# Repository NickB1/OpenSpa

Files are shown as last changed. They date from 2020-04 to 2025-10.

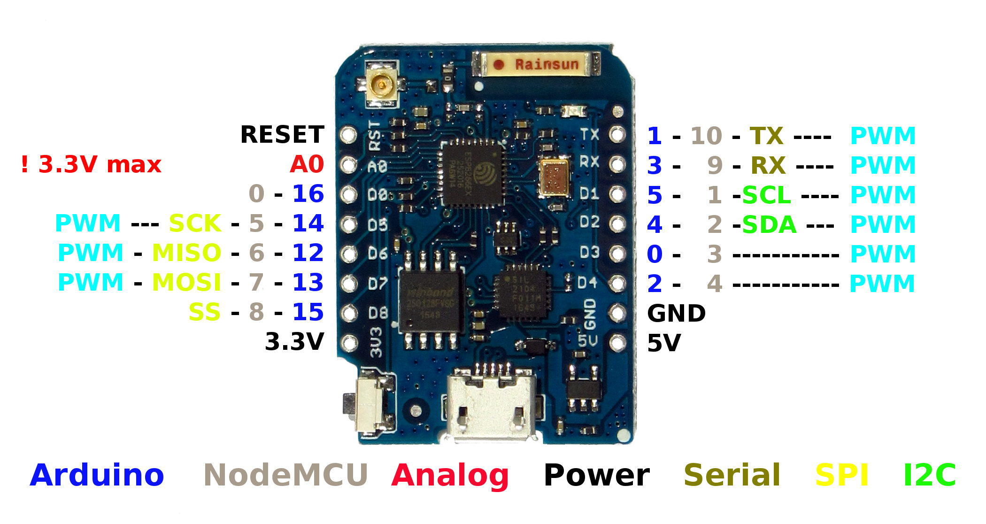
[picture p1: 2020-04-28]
documents/Wemos/Wemos_D1_Mini_Pro_Pinout.jpg

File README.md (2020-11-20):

# OpenSpa
An open source hot tub controller using the ESP8266 (WeMos).

works with MQTT Homie (https://homieiot.github.io/)

Built on ESP8266 Arduino core v2.7.0

More information: https://hackaday.io/project/171003-openspa

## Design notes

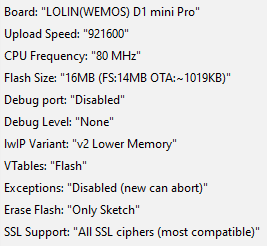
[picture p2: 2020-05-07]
firmware/_openspa/esp8266 settings/OpenSpa_esp8266_settings.png

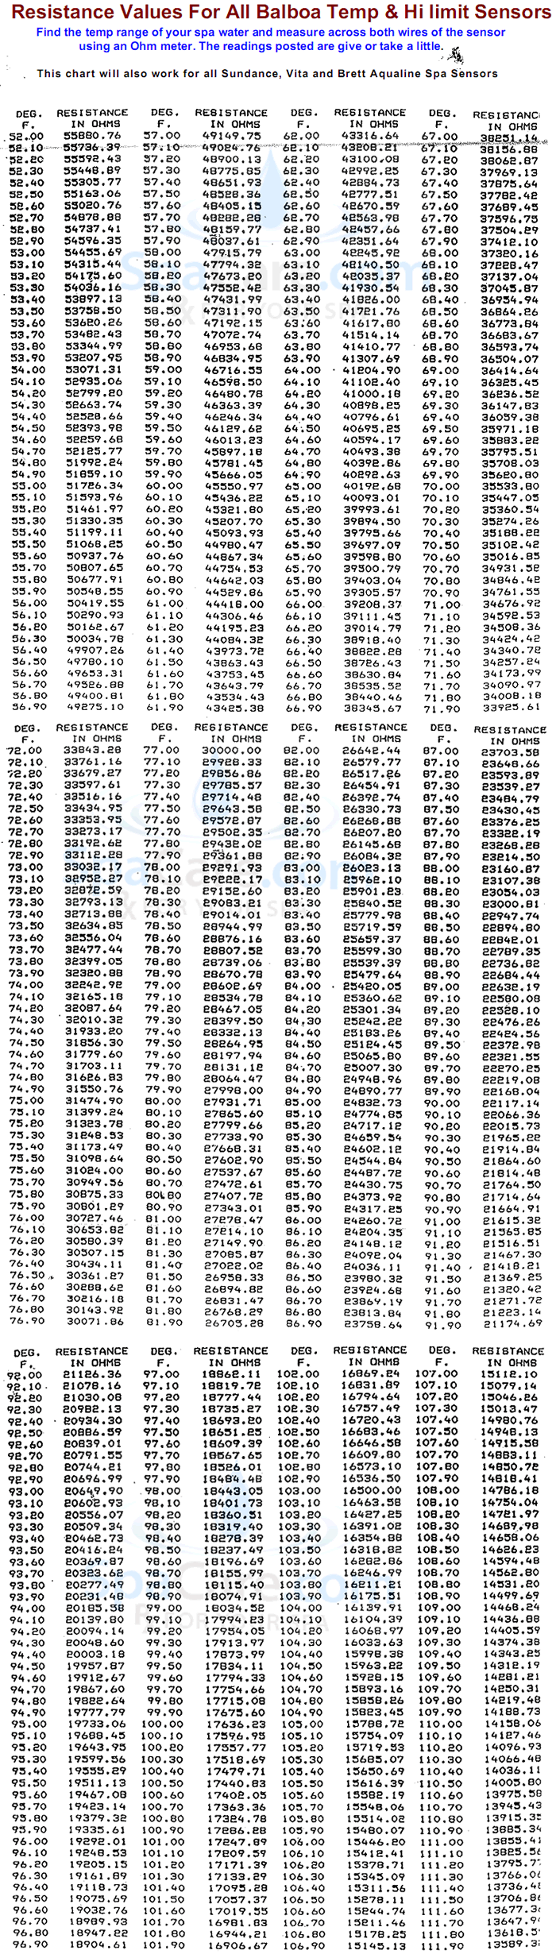
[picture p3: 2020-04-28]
documents/Balboa/Balboa_Resistance_Chart.gif

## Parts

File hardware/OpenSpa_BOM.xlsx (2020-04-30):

Designator | Value | Manufacturer | Part Number | Package | Quantity
C1, C2, C3, C4, C5, C6, C7, C8, C9, C10, C11, C14, C15, C17, C22, C23, C24 | 0.1uF | Kemet | C0603C104K3RAC7411 | 0603 | 17
C12, C21 | 1uF | Kemet | C0603C105K4PACTU | 0603 | 2
C13, C16 | 10uF | Murata | GRT31CR61H106KE01L | 1206 | 2
C18, C19 | 22uF | Kemet | C1206C226M8RACTU | 1206 | 2
C20 | 75pF | Kemet | C0603C750J5GACTU | 0603 | 1
CON1 |  | Wurth Elektronik | 615008143721 | TH | 1
CON2, CON3, CON4, CON5 |  | Wurth Elektronik | 691236510003 x 3 | TH | 4
D1 |  | ON Semiconductor | BAT54T1G | SOD-123 | 1
D2 |  | Diodes Incorporated | B160-13-F | DO-214AC | 1
D3, D4 |  |  | DNP |  | 2
L1 | 15uH | Wurth Elektronik | 7447714150 | 1050 | 1
LED1, LED3 | Green | Wurth Elektronik | 150080VS75000 | 0805 | 2
LED2 | Red | Wurth Elektronik | 150080RS75000 | 0805 | 1
P1 | 10.0K | Bourns | 3296W-1-103LF | 3296 | 1
Q1 |  | Vishay | SUD50N04-8M8P-4GE3 | TO-252 | 1
R1, R2, R4, R5, R6, R7, R11, R14 | 5.10K | Vishay | CRCW06035K10FKEA | 0603 | 8
R3, R10, R15, R27 | 10.0K | Vishay | CRCW060310K0FKEAHP. | 0603 | 4
R8 | 100K | Vishay | CRCW0603100KFKEAHP | 0603 | 1
R9, R19, R23, R24, R25, R26 | 1.00K | Vishay | CRCW06031K00JNEA | 0603 | 6
R12, R13, R16, R17, R20 | 2.20K | Vishay | CRCW06032K20FKEA | 0603 | 5
R18 | 49.9E | Vishay | CRCW060349R9FKEA | 0603 | 1
R21 | 100K | Vishay | CRCW0603100KFKEA | 0603 | 1
R22 | 13.3K | Vishay | CRCW060313K3FKEA | 0603 | 1
SW1 |  | TE Connectivity | 1825910-6 | TH | 1
U1, U3 |  | Texas Instruments | LM321MF/NOPB | SOT-23-5 | 2
U2 |  | Texas Instruments | TL331IDBVR | SOT-23-5 | 1
U4, U5, U6 |  | Texas Instruments | SN74LVC1G125DCK | SC-70-5, SC-88A, SOT-323-5, SOT-353, 5-TSSOP | 3
U7 |  | Texas Instruments | PCA9515BDGKR | VSSOP-8 | 1
U8 |  | Microchip | MCP23017T-E/SO | SOIC-28 | 1
U9 |  | Microchip | MCP1700T-3302E/TT | SOT-23-3 | 1
U10 |  | Wemos | D1 mini Pro |  | 1
U11 | Original: TI SN74LVC1G02DBV | Nexperia | 74LVC1G02GV,125 | SC-74A-5 | 1
U12 |  | Texas Instruments | TPS54308DDCT | TSOT-23-6 | 1
U13 |  | Texas Instruments | ULN2803ADWR | SOIC-16 | 1
U14 |  | Texas Instruments | TXS0101DBVR | SOT-23-6 | 1
U15 |  | Maxim | DS18B20+ | TO-92 | 1

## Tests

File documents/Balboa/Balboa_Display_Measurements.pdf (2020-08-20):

# Balboa Display

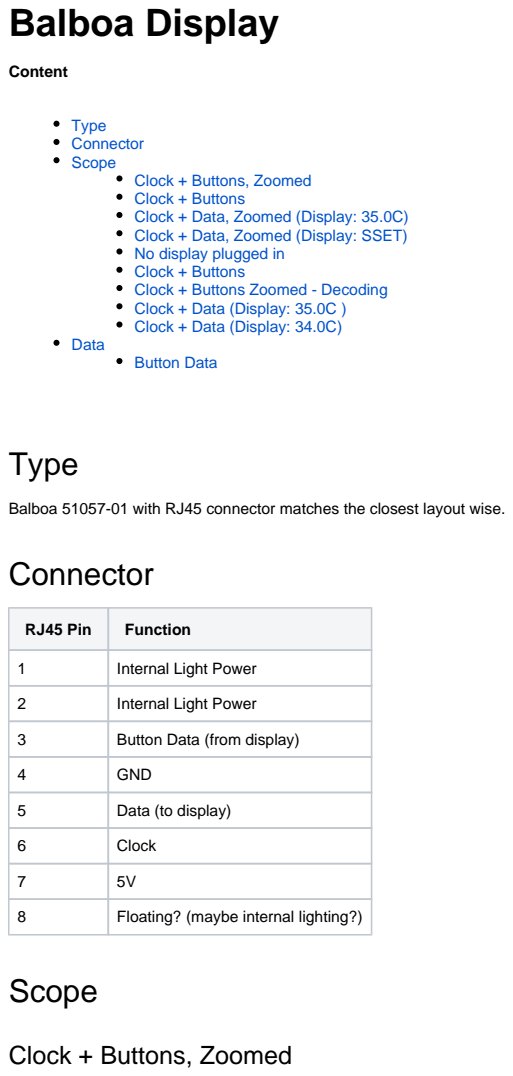
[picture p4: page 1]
Content; Type Connector Scope; Data; Button Data; Type; RJ45 Pin; Function; Internal Light Power; Button Data (from display); GND; Data (to display); Clock; Floating? (maybe internal lighting?); Scope

Clock + Buttons, Zoomed
Clock + Buttons
Clock + Data, Zoomed (Display: 35.0C)
Clock + Data, Zoomed (Display: SSET)
No display plugged in
Clock + Buttons Zoomed - Decoding
Clock + Data (Display: 35.0C )
Clock + Data (Display: 34.0C)

Balboa 51057-01 with RJ45 connector matches the closest layout wise.
Connector

## Clock + Buttons

## Clock + Data, Zoomed (Display: 35.0C)

## Clock + Data, Zoomed (Display: SSET)

## No display plugged in

## Clock + Buttons

## Clock + Buttons Zoomed - Decoding

Button | Decoding
Temp Up | 100

Temp Down 101

Light | 111
Jets | 110
Blower | 011

## Clock + Data (Display: 35.0C )

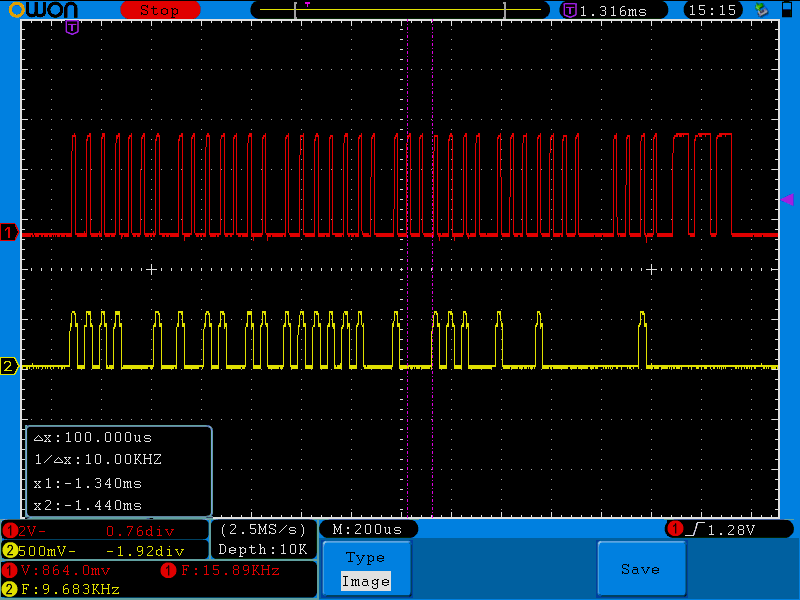
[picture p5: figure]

## Clock + Data (Display: 34.0C)

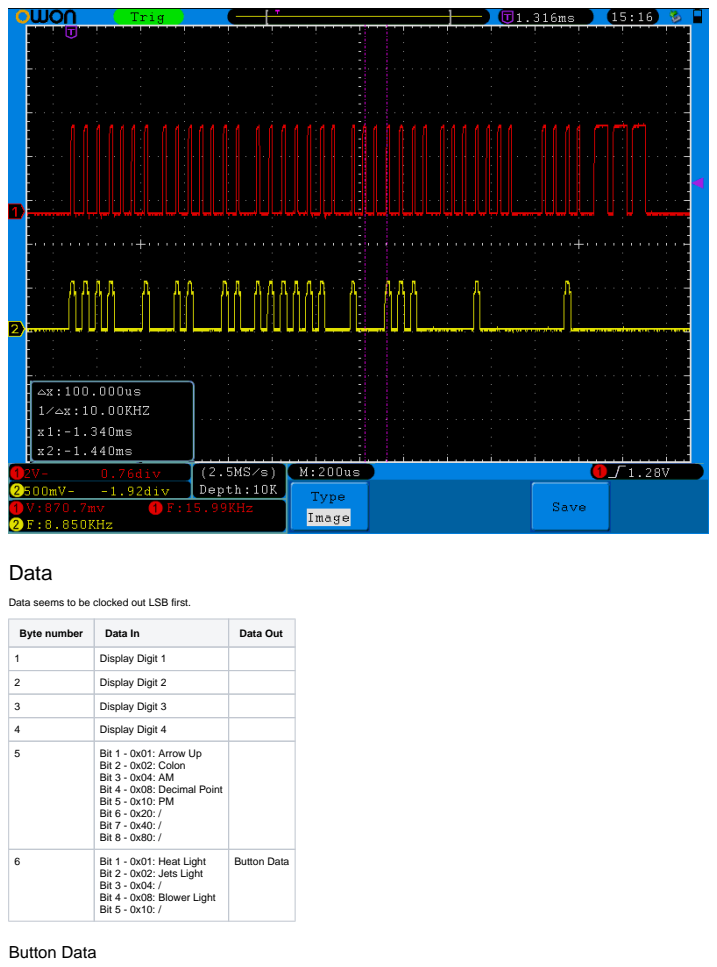
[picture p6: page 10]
Data; Byte number; Data In; Data Out; Display Digit 1; Display Digit 2; Display Digit 3; Display Digit 4; Bit 1 - 0x01: Arrow Up; Bit 1 - 0x01: Heat Light; Button Data

Data seems to be clocked out LSB first.

Bit 2 - 0x02: Colon
Bit 3 - 0x04: AM
Bit 4 - 0x08: Decimal Point
Bit 5 - 0x10: PM
Bit 6 - 0x20: /
Bit 7 - 0x40: /
Bit 8 - 0x80: /

Bit 2 - 0x02: Jets Light
Bit 3 - 0x04: /
Bit 4 - 0x08: Blower Light
Bit 5 - 0x10: /

Function | MSB First | LSB First
Temp Up | 0x04 | 0x10
Temp Down | 0x05 | 0x50
Lights (3 settings) 0x07 | 0x70
Jets (2 settings) | 0x06 | 0x30
Blower | 0x03 | 0x60

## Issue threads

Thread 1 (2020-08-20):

Question

tmjo, 2020-08-20:
Hi @NickB1,

Sorry for opening this as an issue, it's more of a question, and I hope you don't mind me asking here. I'm following your OpenSpa and also the balboa-spa-mqtt-controller projects trying to do something similar. My controller is (still) working but is a decade old. If it fails, I'll try do implement a solution similar to OpenSpa, but meanwhile I would like to connect my spa to get status and control if with an ESP8266.

My spa is a Balboa HSEX2000 Mach3 (part no 54503-01) and is branded GL2000 inside a plastic enclosure (know there is a different variant of the same with metallic enclosure). Display is ML400.

Would you mind me asking which display is connected to yours? And do you know the type of controller that was originally fit to it? I see you mentioned 25501 on hackaday.io, would you mind sharing some more details?

I was initially trying to use the information found [here](https://github.com/ccutrer/balboa_worldwide_app), but found out my spa has a 8-pin Molex connector to the display and not 4-pin as is the case for the referenced project which is RS485 based. See particularly [this issue](https://github.com/ccutrer/balboa_worldwide_app/issues/14) if you're interested. Although yours is a RJ45, I was hoping it would be similar to mine, just different connector.

Anything you could share that could help me shed some light on my issue? Protocol? Connections?

Thanks in advance.

NickB1, 2020-08-20:
Hi,

No problem.
At first glance the HSEX2000 Mach3 seems to be fairly newer then my original 25501 board.
The Balboa 51057-01 display seems to match my display the closest (the spa manufacturer has stuck another layout over it with their logo).

I've committed my findings about the display protocol in the documents folder.
It's best to leave the display plugged in and probe the lines with a scope.
My controller just outputted a single clock pulse without any data when no display was plugged in.
It waited for the data in line to go high before outputting the full clock train with data.

tmjo, 2020-08-20:
Thanks a lot! I believe this information will help me a lot in deciphering my spa. I'll try to connect a oscilloscope and measure one of the next weeks when I'm back at work and have one available. Even if the models are different, I guess they don't change the protocols every second day, so since mine is not a match with the newer series (4-pin) I really hope they are similar to yours!

Bostwickenator, 2021-10-04:
Hey Nick. I'm also looking into this wanting to emulate the panel side. I don't see in that document if this is using any kind regular serial protocol. It looks like you are just clocking out your data "by hand". I'm thinking from the scope traces it's 3V signaling? It also looks like you are commanding the display segments themselves instead of writing a temperature value and the panel using that to set the segments itself. Did I understand that correctly?

NickB1, 2021-10-05:
>
>
> Hey Nick. I'm also looking into this wanting to emulate the panel side. I don't see in that document if this is using any kind regular serial protocol. It looks like you are just clocking out your data "by hand". I'm thinking from the scope traces it's 3V signaling? It also looks like you are commanding the display segments themselves instead of writing a temperature value and the panel using that to set the segments itself. Did I understand that correctly?

Hi, you can see some scope screenshot of the protocol here:
https://github.com/NickB1/OpenSpa/blob/master/documents/Balboa/Balboa_Display_Measurements.pdf
It's not a regular uart, it's a custom data/clock protocol where individual display segments data and button data is clocked through.
Maybe newer displays use a regular uart but I don't have any experience with these.

Bostwickenator, 2021-10-05:
Thanks for the reply. I was looking at the screenshots but was having a
little trouble figuring out a few parameters for instance in (clock +
data), zoomed (display: 35.0C) there appear to be three signal levels for
the data line but I don't see any references to that in your protocol
implementation. Is that just an artifact of the scope? It looks like the
clock signal is 4V and data is only 500mV? I read the OWON scope manual it
that seems to be how I should interpret the screenshots. Those values just
seem a little odd so I thought I'd reach out and ask. Thanks for the help
of even posting this it's invaluable.

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

NickB1, 2021-10-05:
Good catch, I think the multiplier on the data channel of the scope was not configured to be the same as the probe (probable should be x10).
Both signals have a logic level of 5V.
Here is a snippet of the schematic where the level conversion to 3.3V happens to interface it with the esp8266.

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

netmindz, 2022-01-17:
The VL series isn't compatible with the GL controllers @tmjo not sure why not. So they may or may not share the same protocol. I'll have to hook up the scope and see what we get

Closed 2021-01-27.

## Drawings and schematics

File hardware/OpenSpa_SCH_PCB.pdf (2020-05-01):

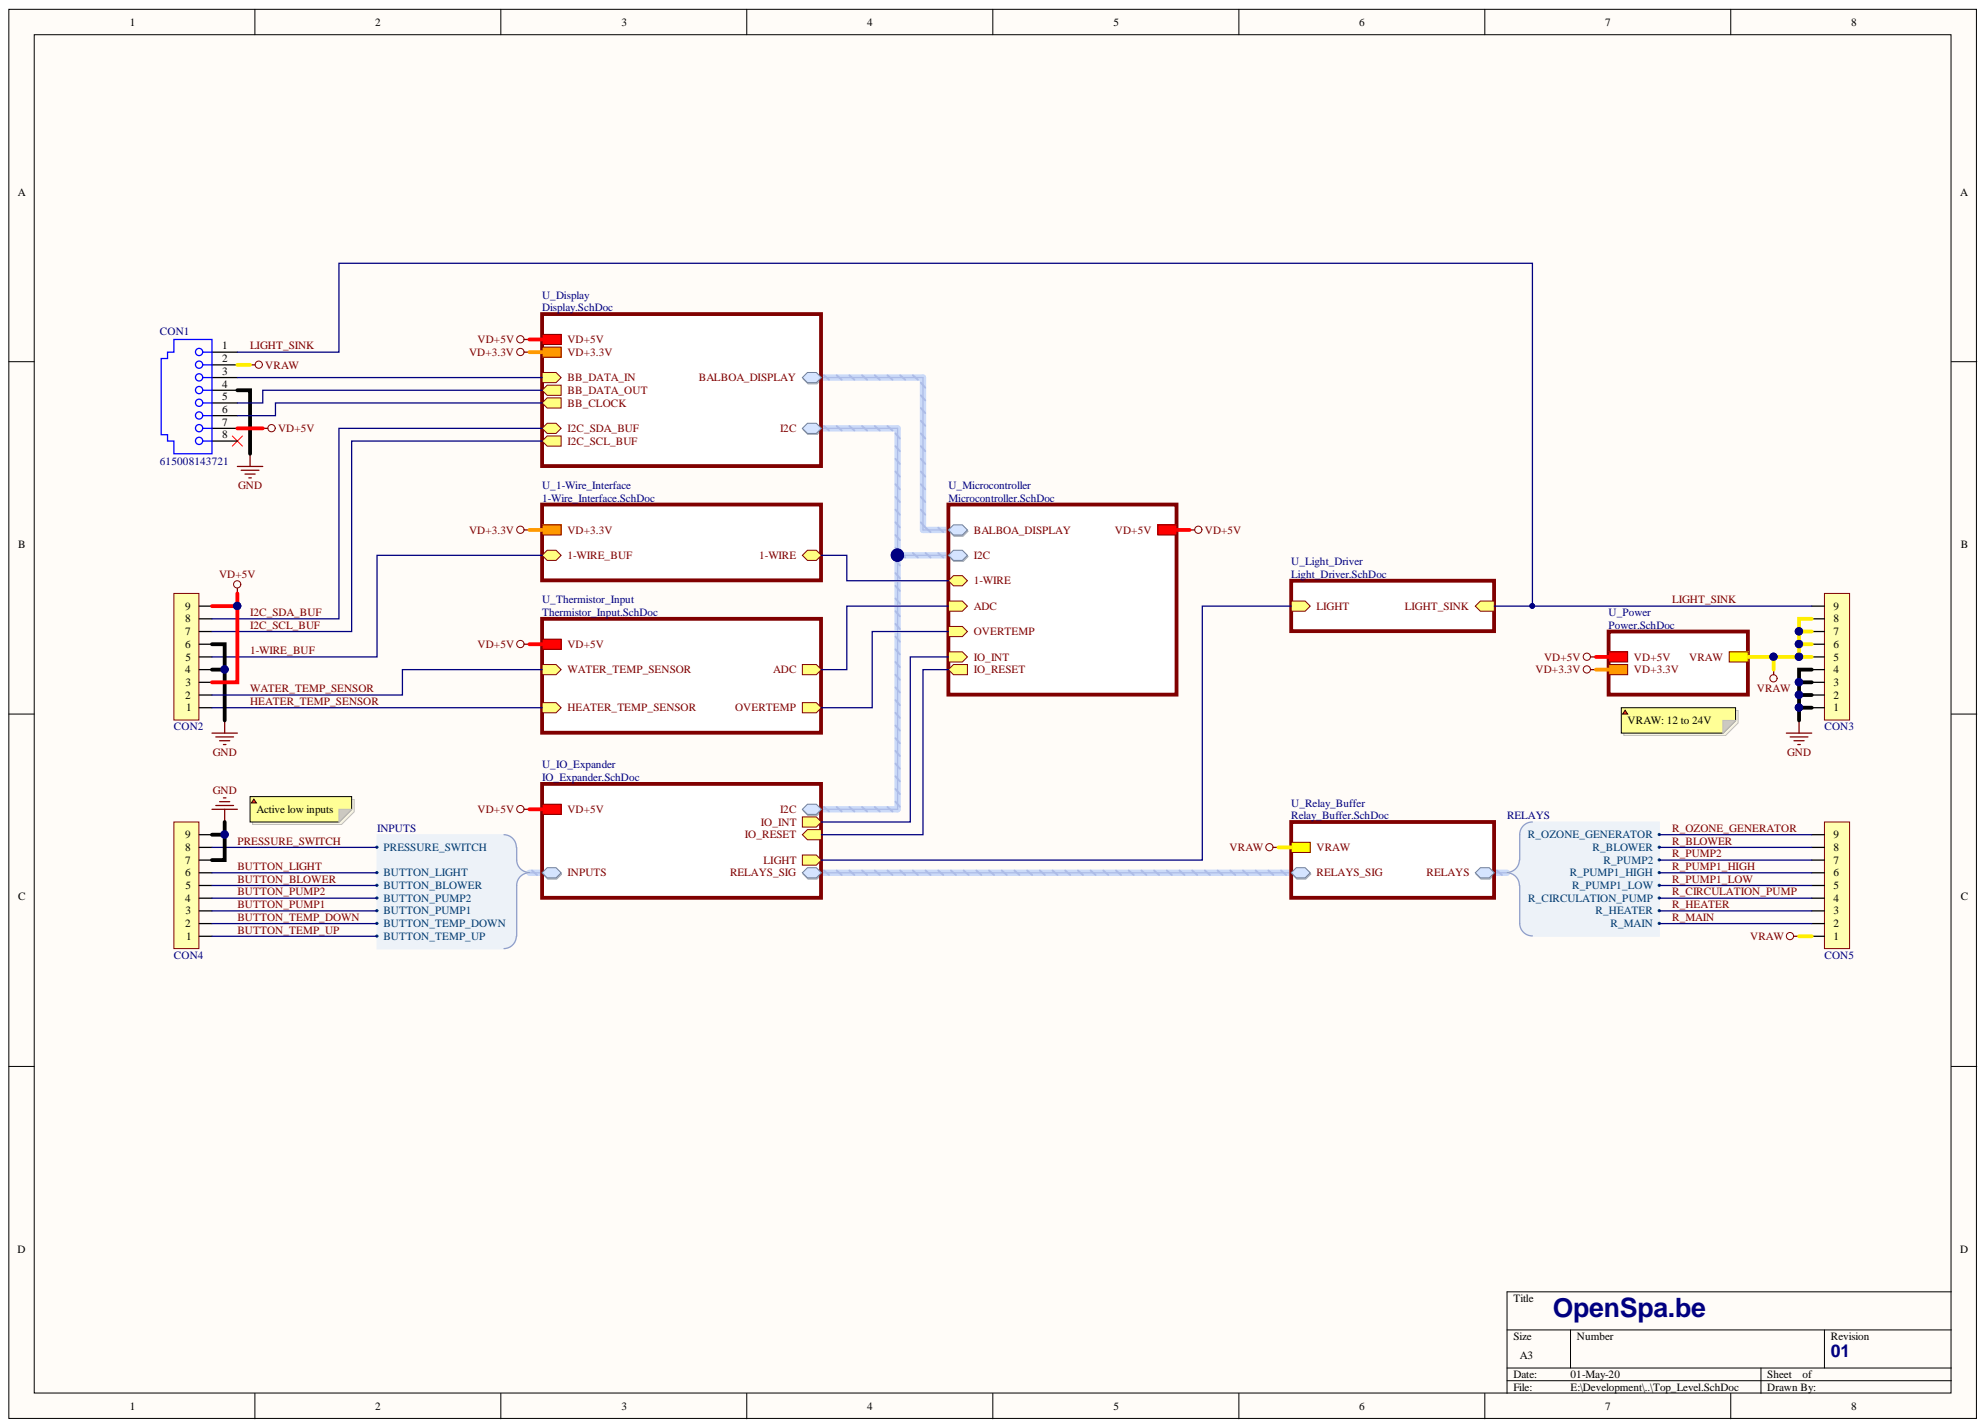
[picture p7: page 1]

VD+5 | V
I 2C_ SDA_ BUF | T h ermisto r_ In p ut.S c hDo c | ADC IO_IN OV ERT EMP T I O _ RES E T | VR AW | U_ P owe r

I 2C_ S C L_ BUF | W ATER _ T EMP _ SEN SOR ADC HE ATER _ T EMP _ S ENSOR OV ERT EMP
VD+5 V 1 -W IRE _BU F

W ATER _ T EMP _ SEN SOR
HE ATER _ T EMP _ S ENSOR

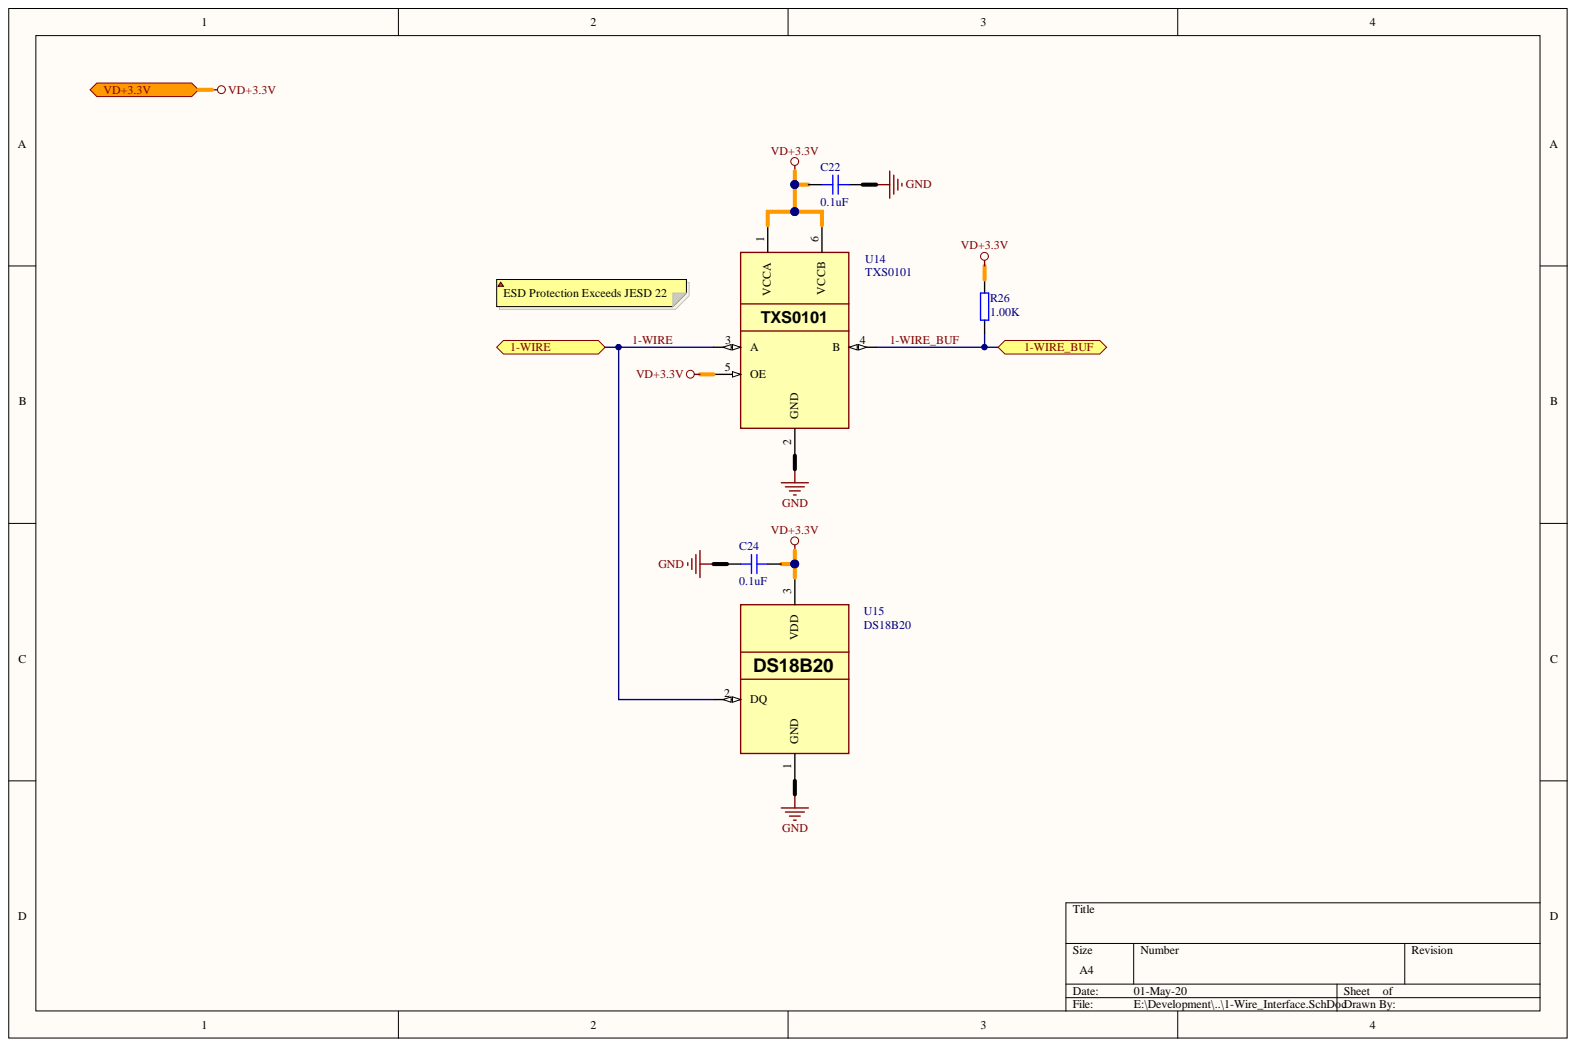
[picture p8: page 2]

ESD Protection Exceeds JESD 22

Size A4 | Number | Revision

Date: 01-May-20 | Sheet of
File: E:\Development\..\1-Wire_Interface.SchDocDrawn By:

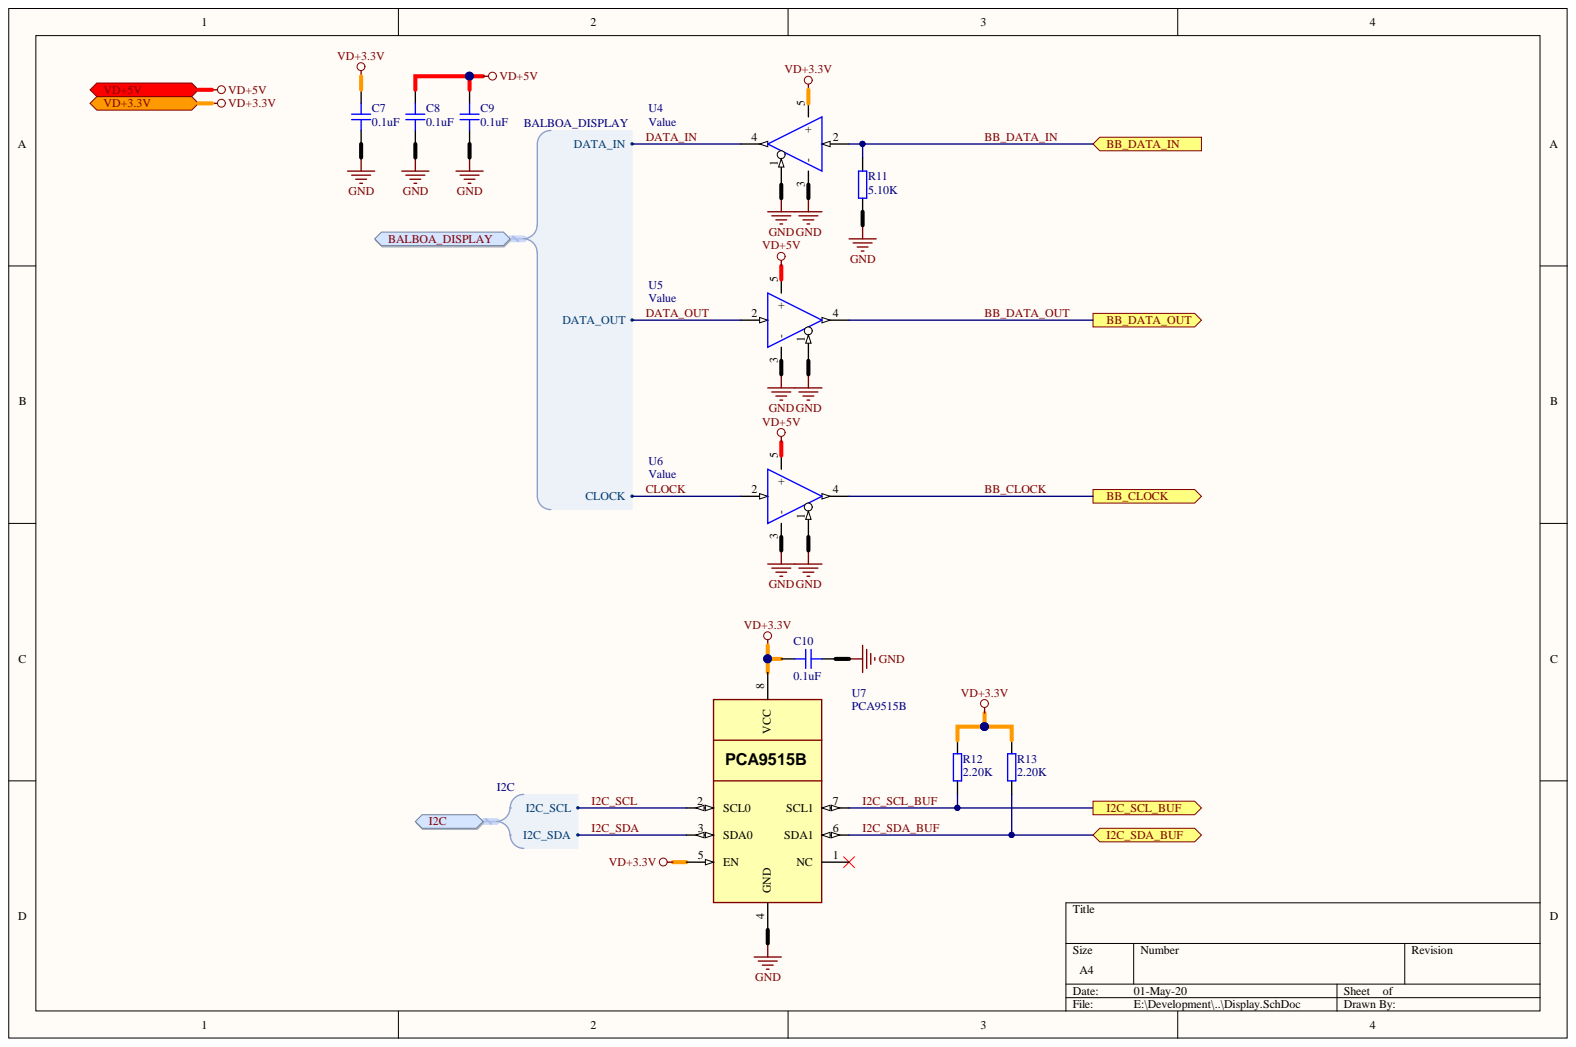
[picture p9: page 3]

Size A4 | Number | Revision

Date: 01-May-20 | Sheet of
File: E:\Development\..\Display.SchDoc | Drawn By:

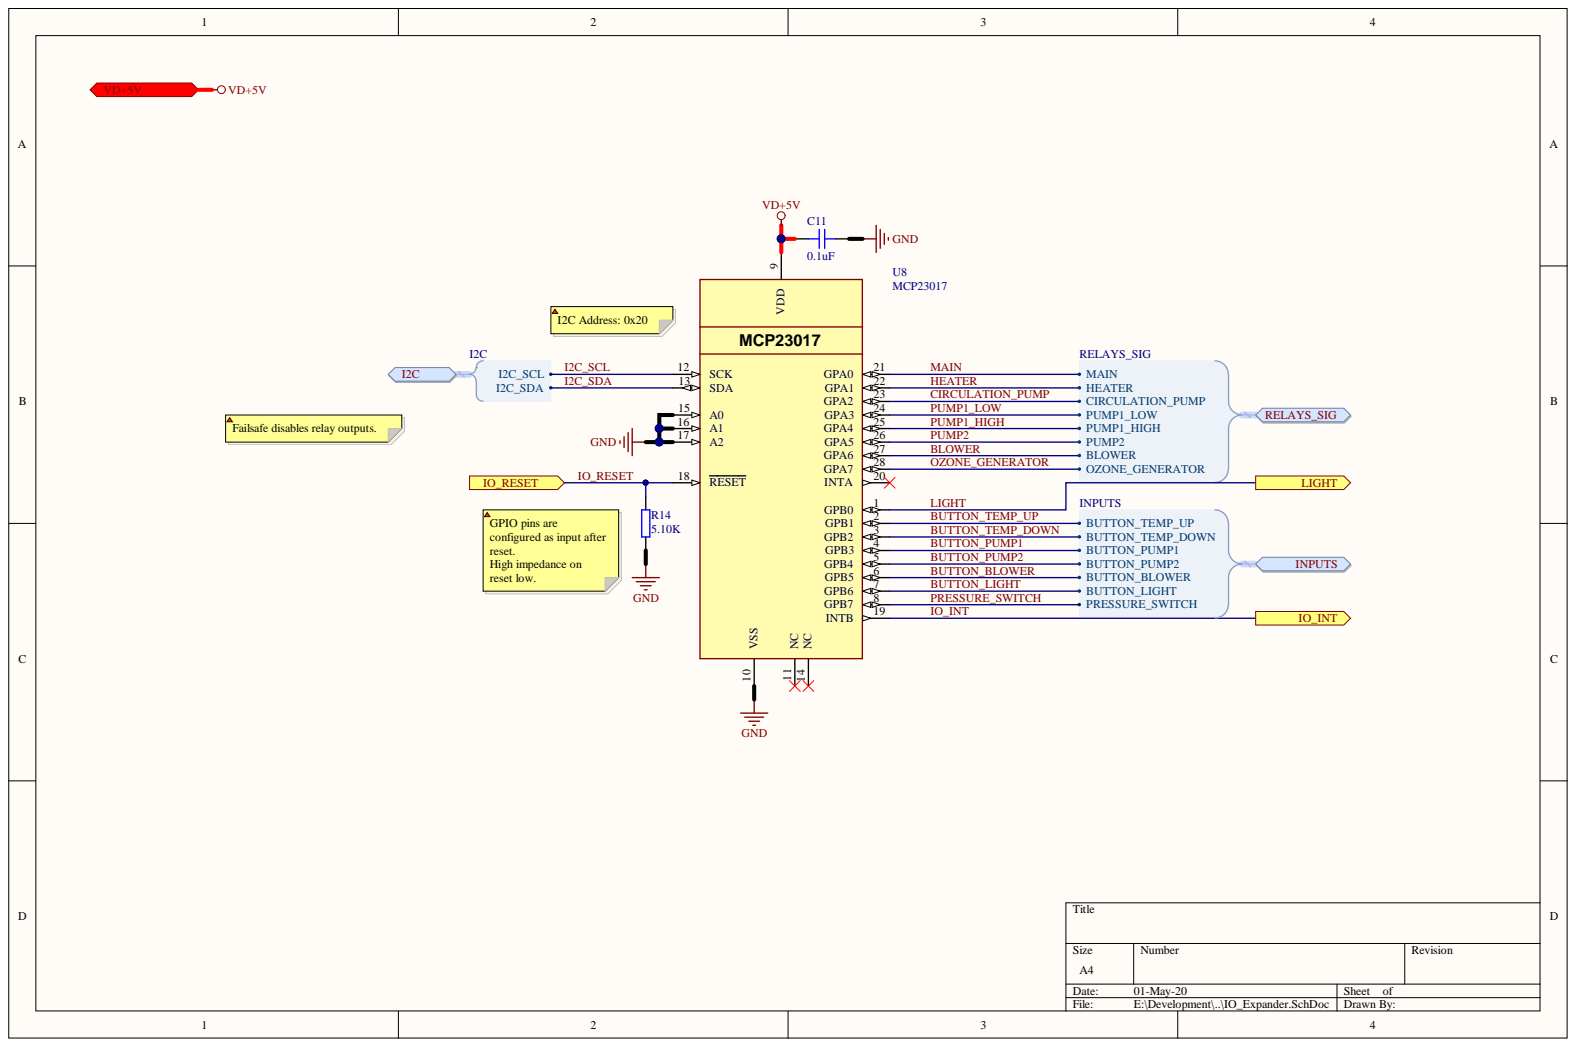
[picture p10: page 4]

Failsafe disables relay outputs.

GPIO pins are
configured as input after
reset.
High impedance on
reset low.

Size A4 | Number | Revision

Date: 01-May-20 | Sheet of
File: E:\Development\..\IO_Expander.SchDoc | Drawn By:

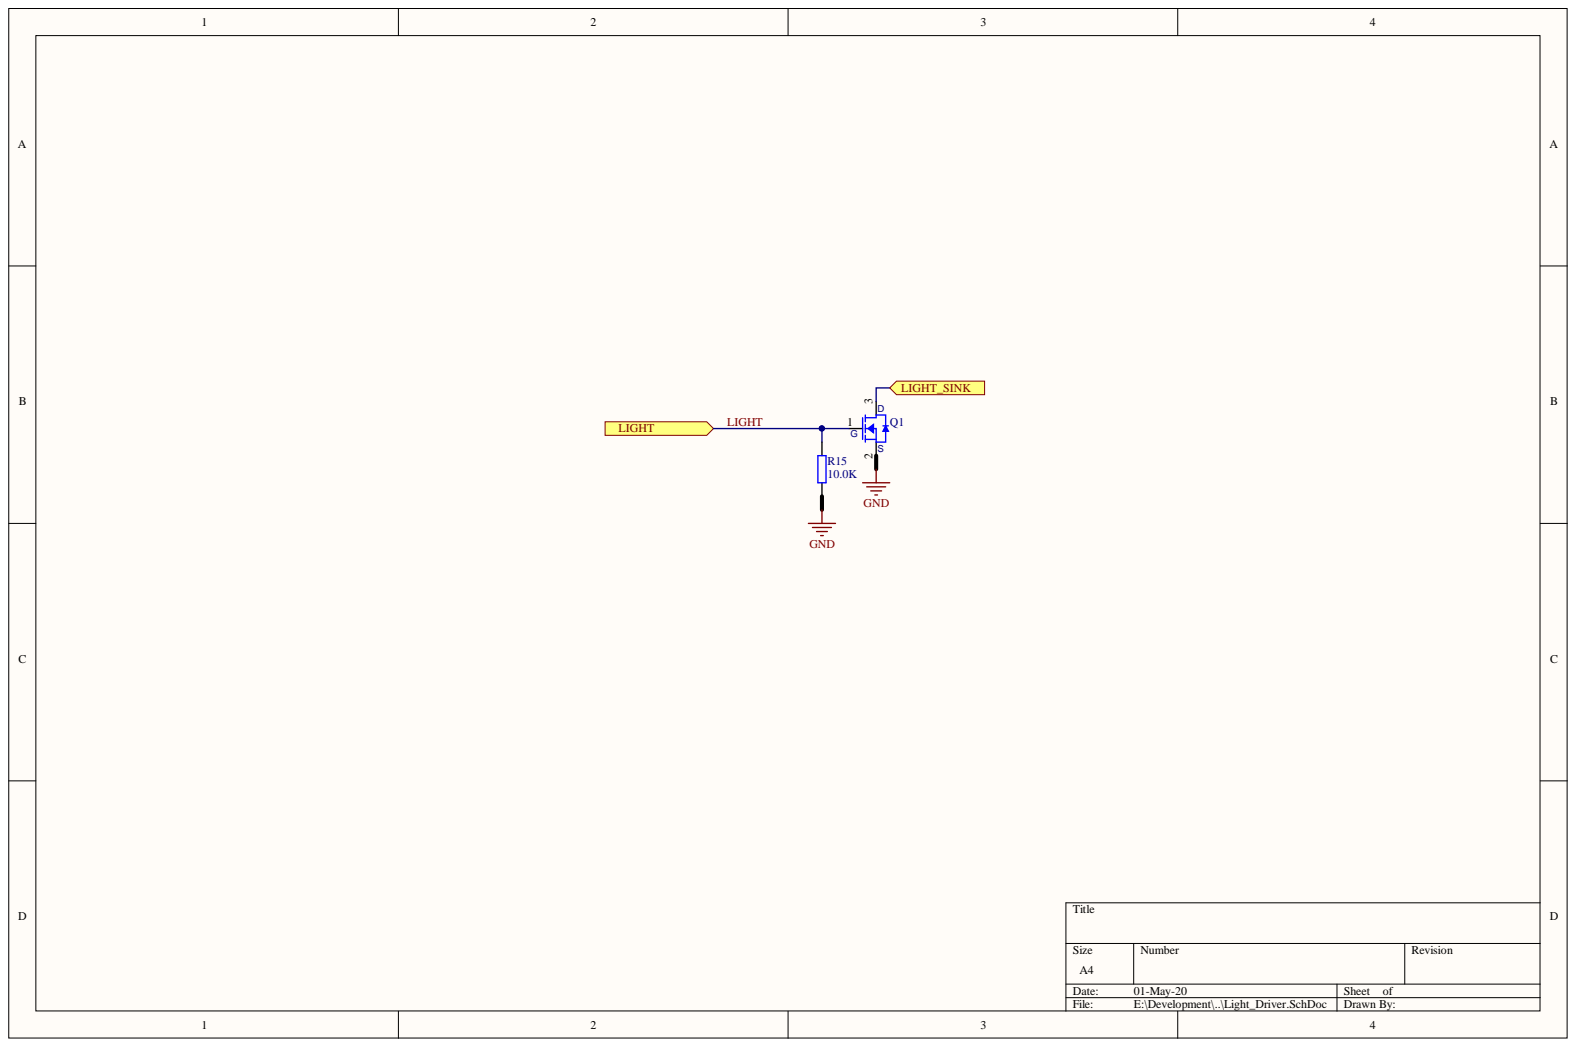
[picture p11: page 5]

Size A4 | Number | Revision

Date: 01-May-20 | Sheet of
File: E:\Development\..\Light_Driver.SchDoc | Drawn By:

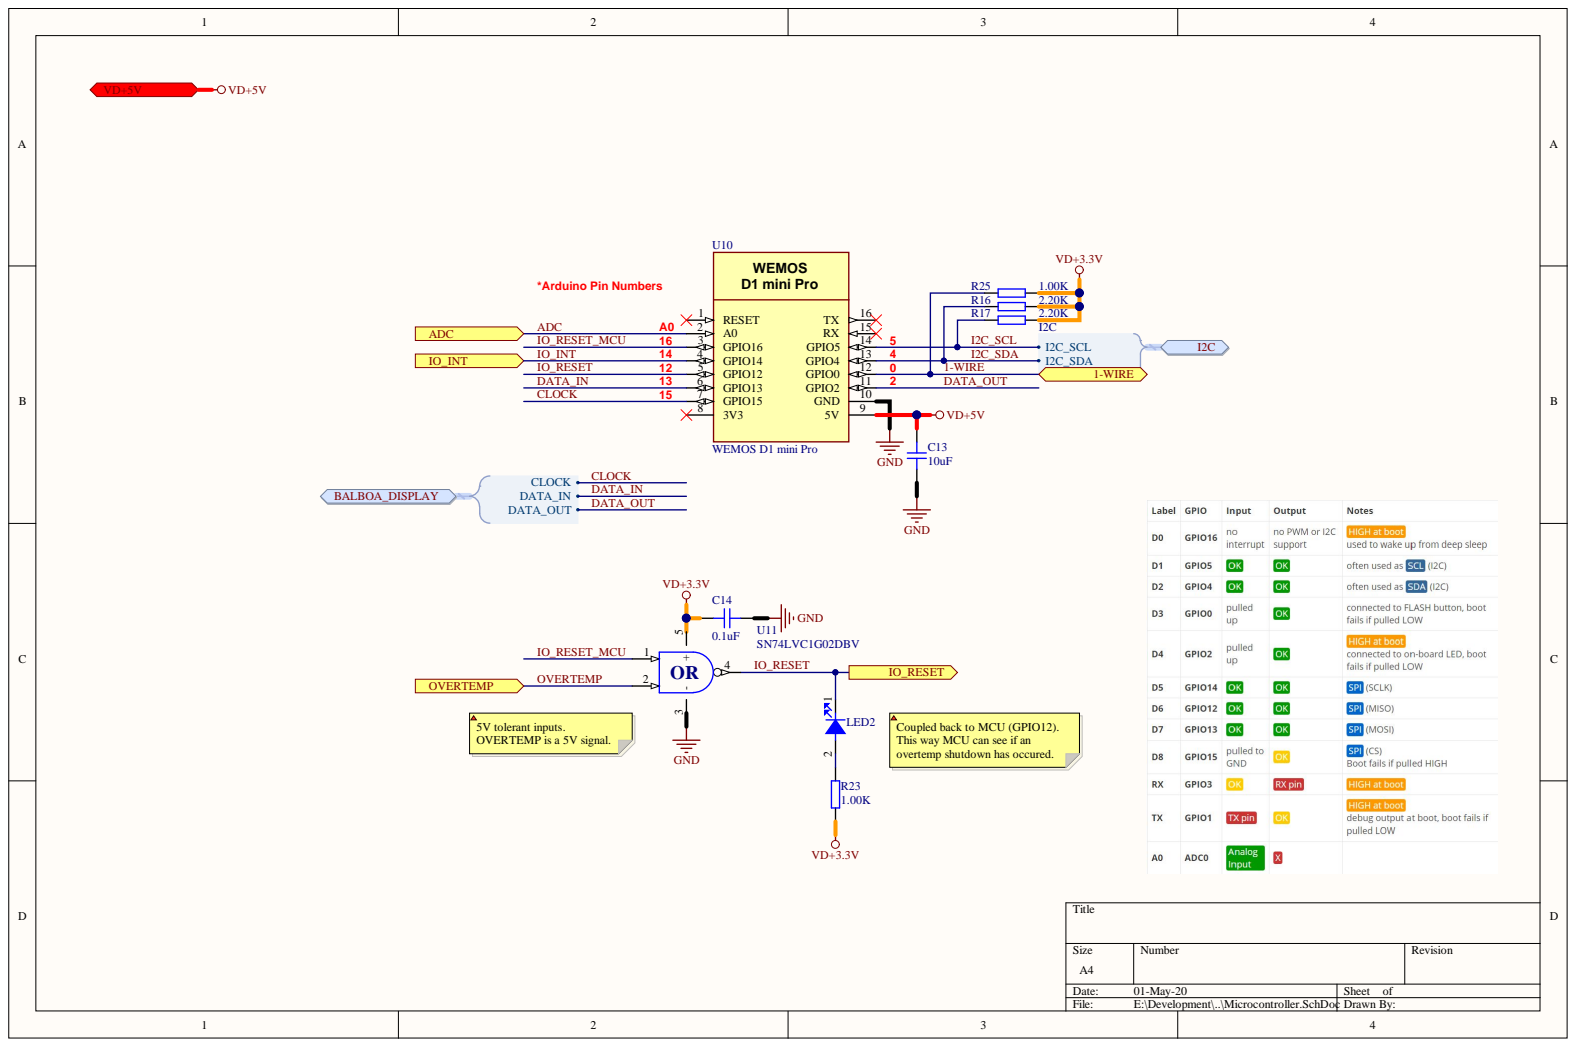
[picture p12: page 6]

Coupled back to MCU (GPIO12).
This way MCU can see if an
overtemp shutdown has occured.

Size A4 | Number | Revision

Date: 01-May-20 | Sheet of
File: E:\Development\..\Microcontroller.SchDoc Drawn By:

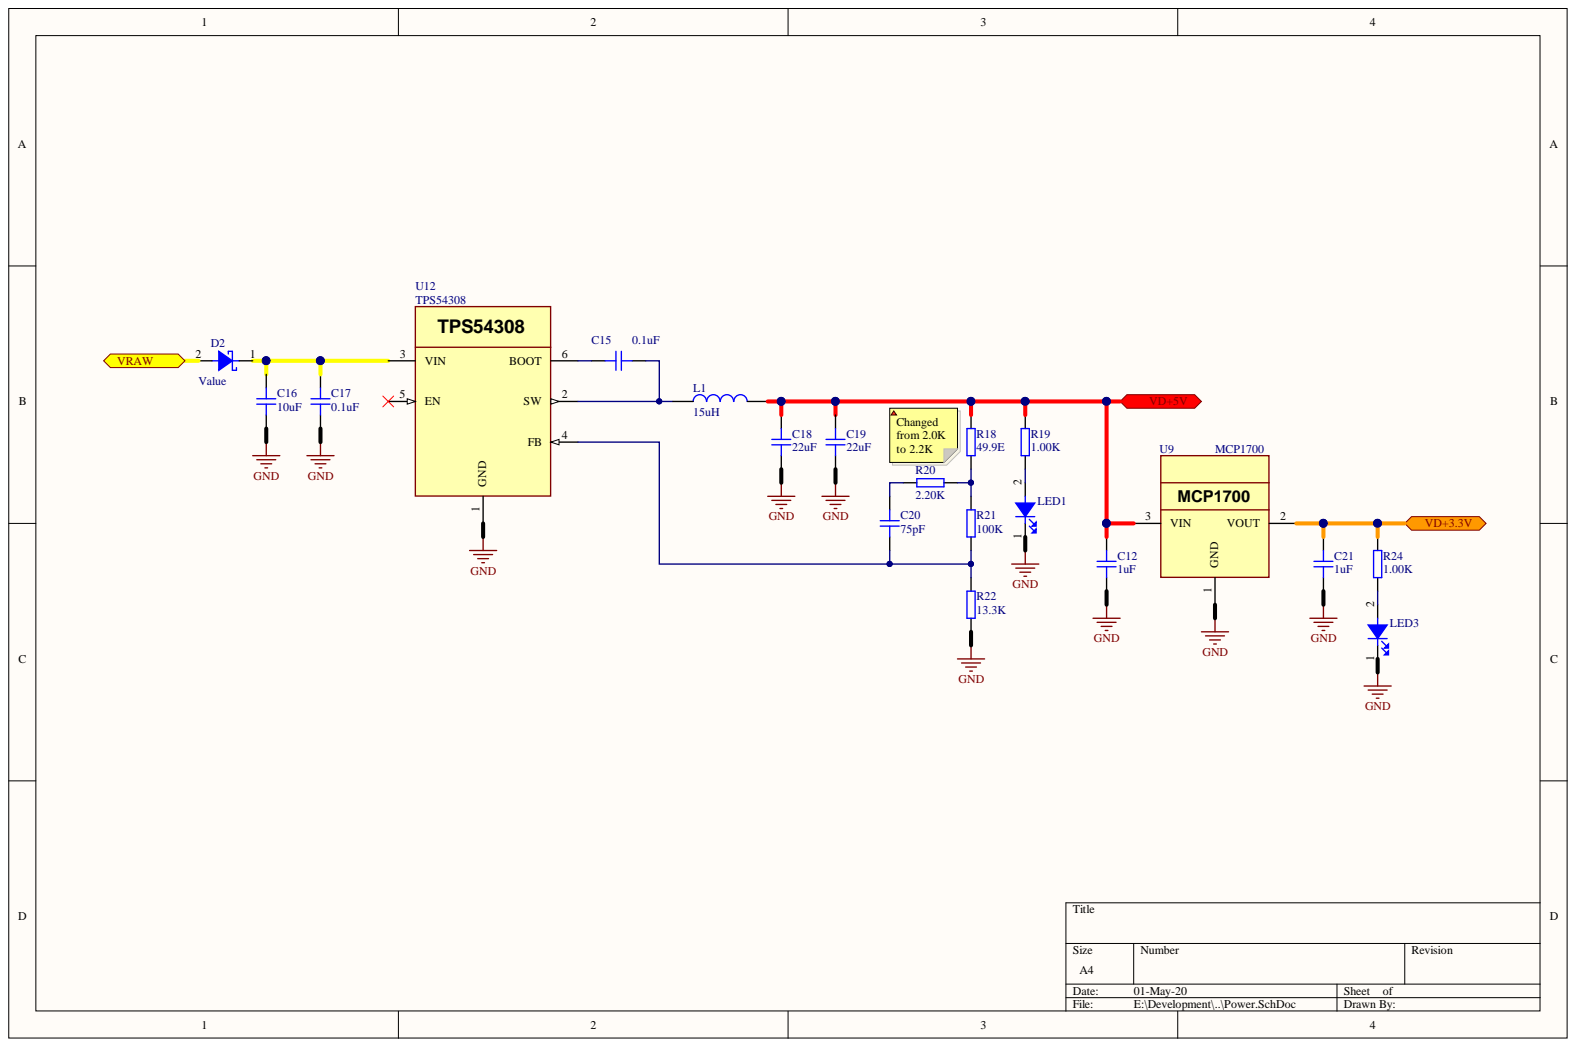
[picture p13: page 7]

S ize A 4 | Number | Rev isi o n

Date: 01-May-20 | S heet o f
F i le: E:\Devel opmen t\. .\Power.SchDo c | Drawn By :

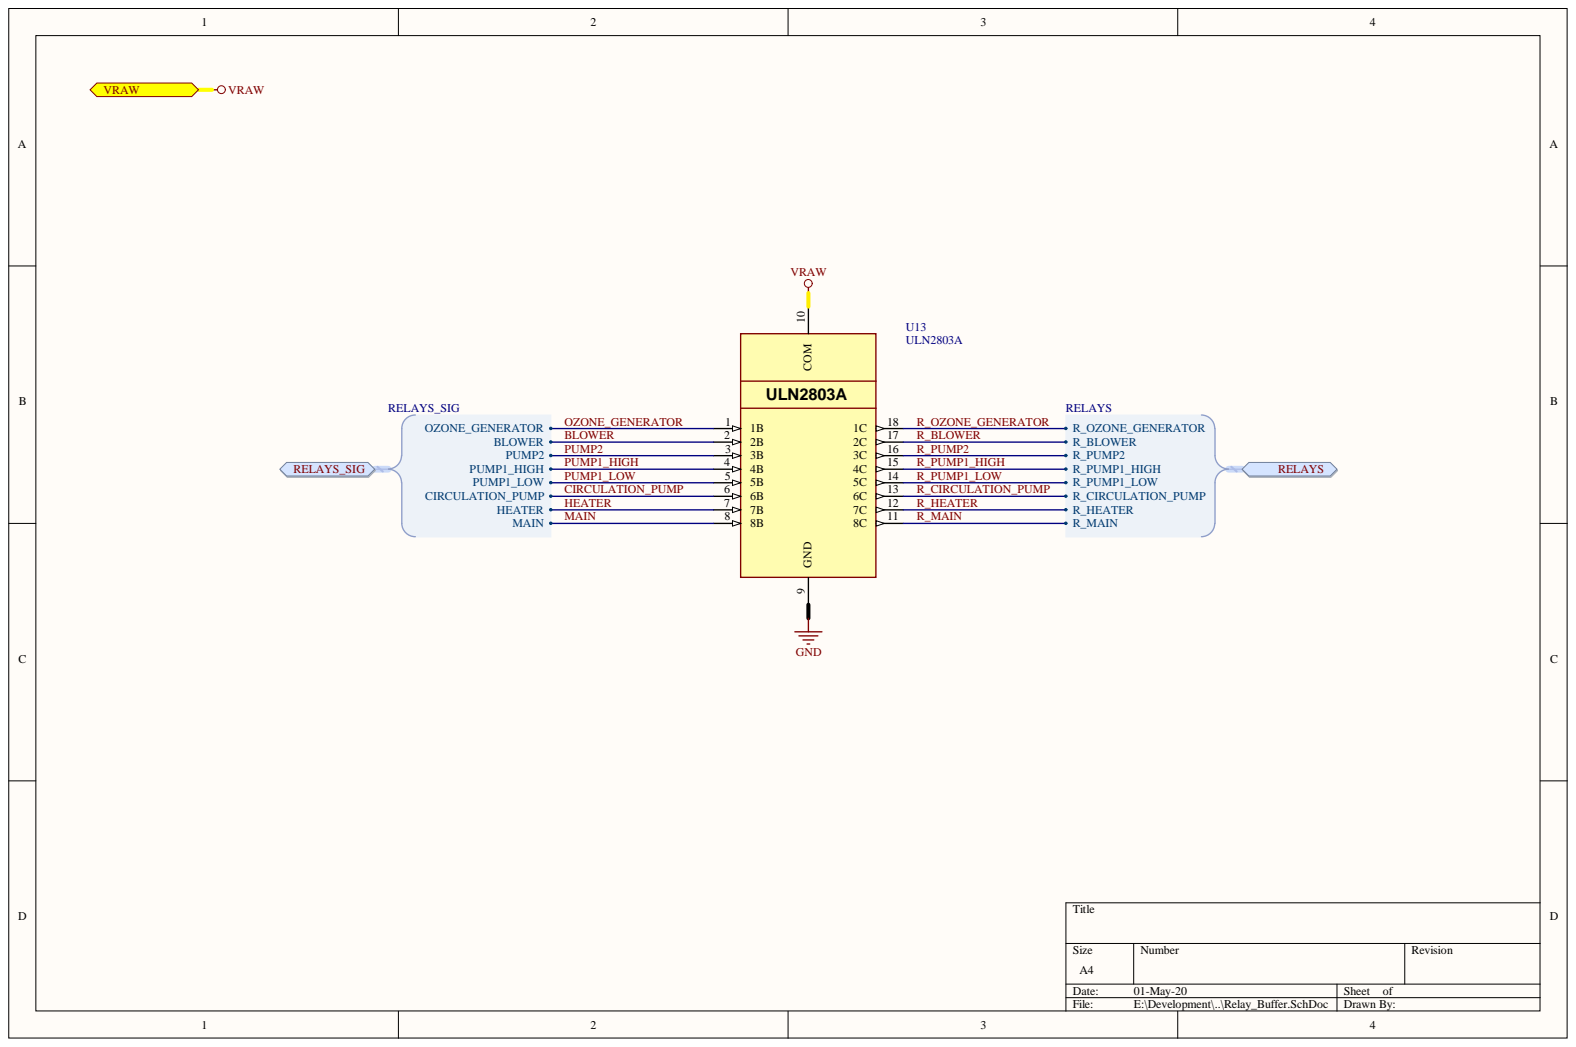
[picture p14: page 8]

Size A4 | Number | Revision

Date: 01-May-20 | Sheet of
File: E:\Development\..\Relay_Buffer.SchDoc | Drawn By:

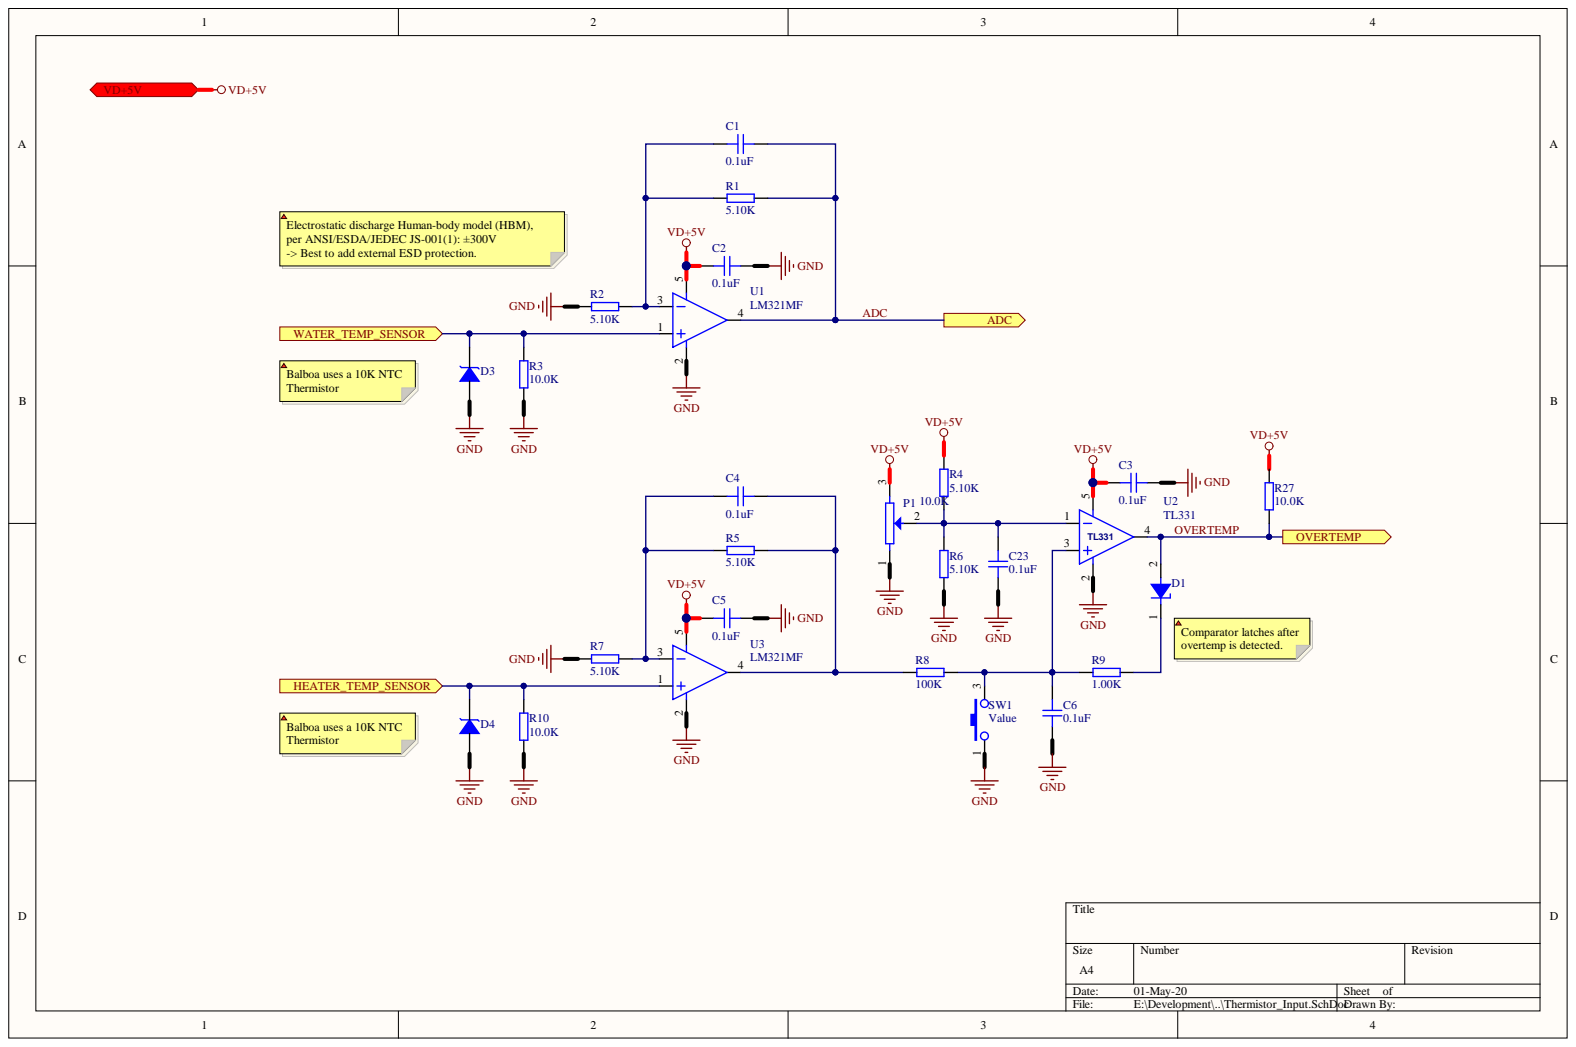
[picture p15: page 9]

Electrostatic discharge Human-body model (HBM),
per ANSI/ESDA/JEDEC JS-001(1): ±300V
-> Best to add external ESD protection.

Size A4 | Number | Revision

Date: 01-May-20 | Sheet of
File: E:\Development\..\Thermistor_Input.SchDoDrawn c | By:

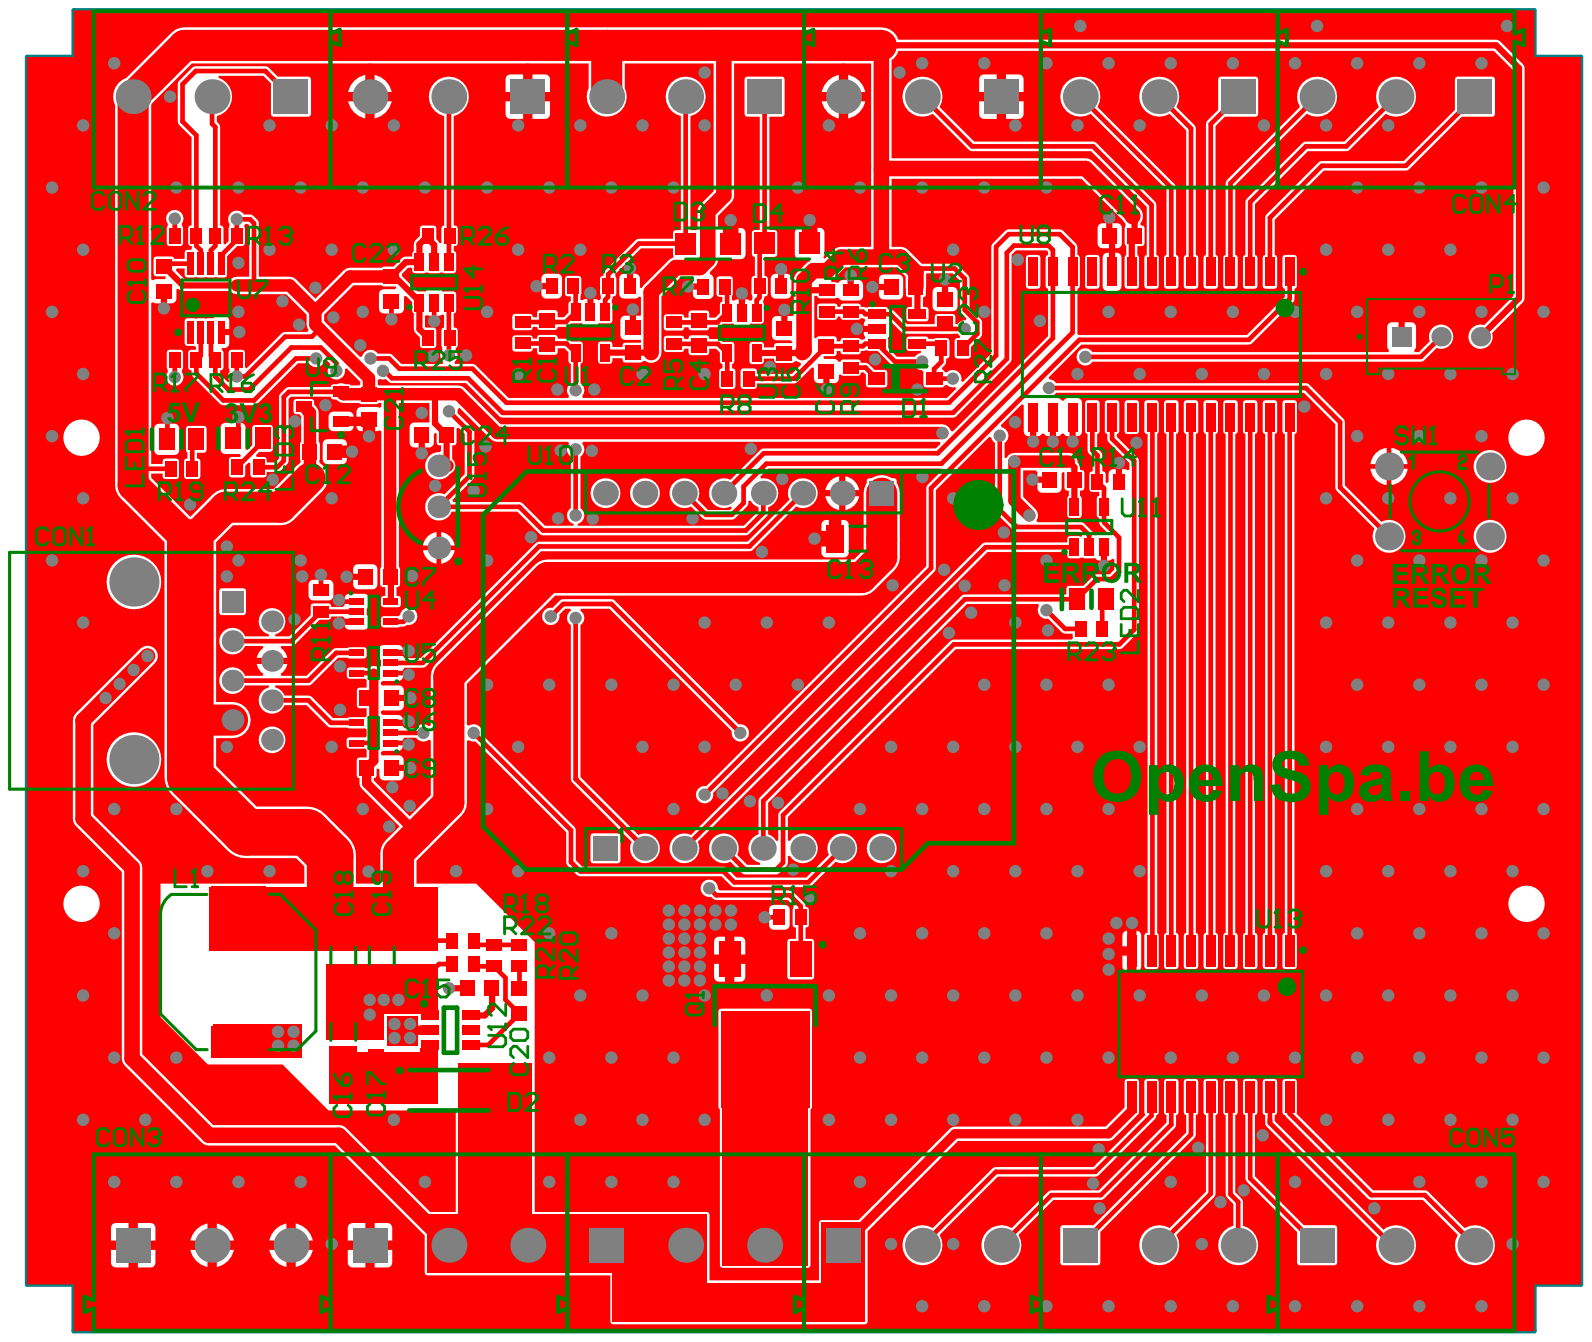
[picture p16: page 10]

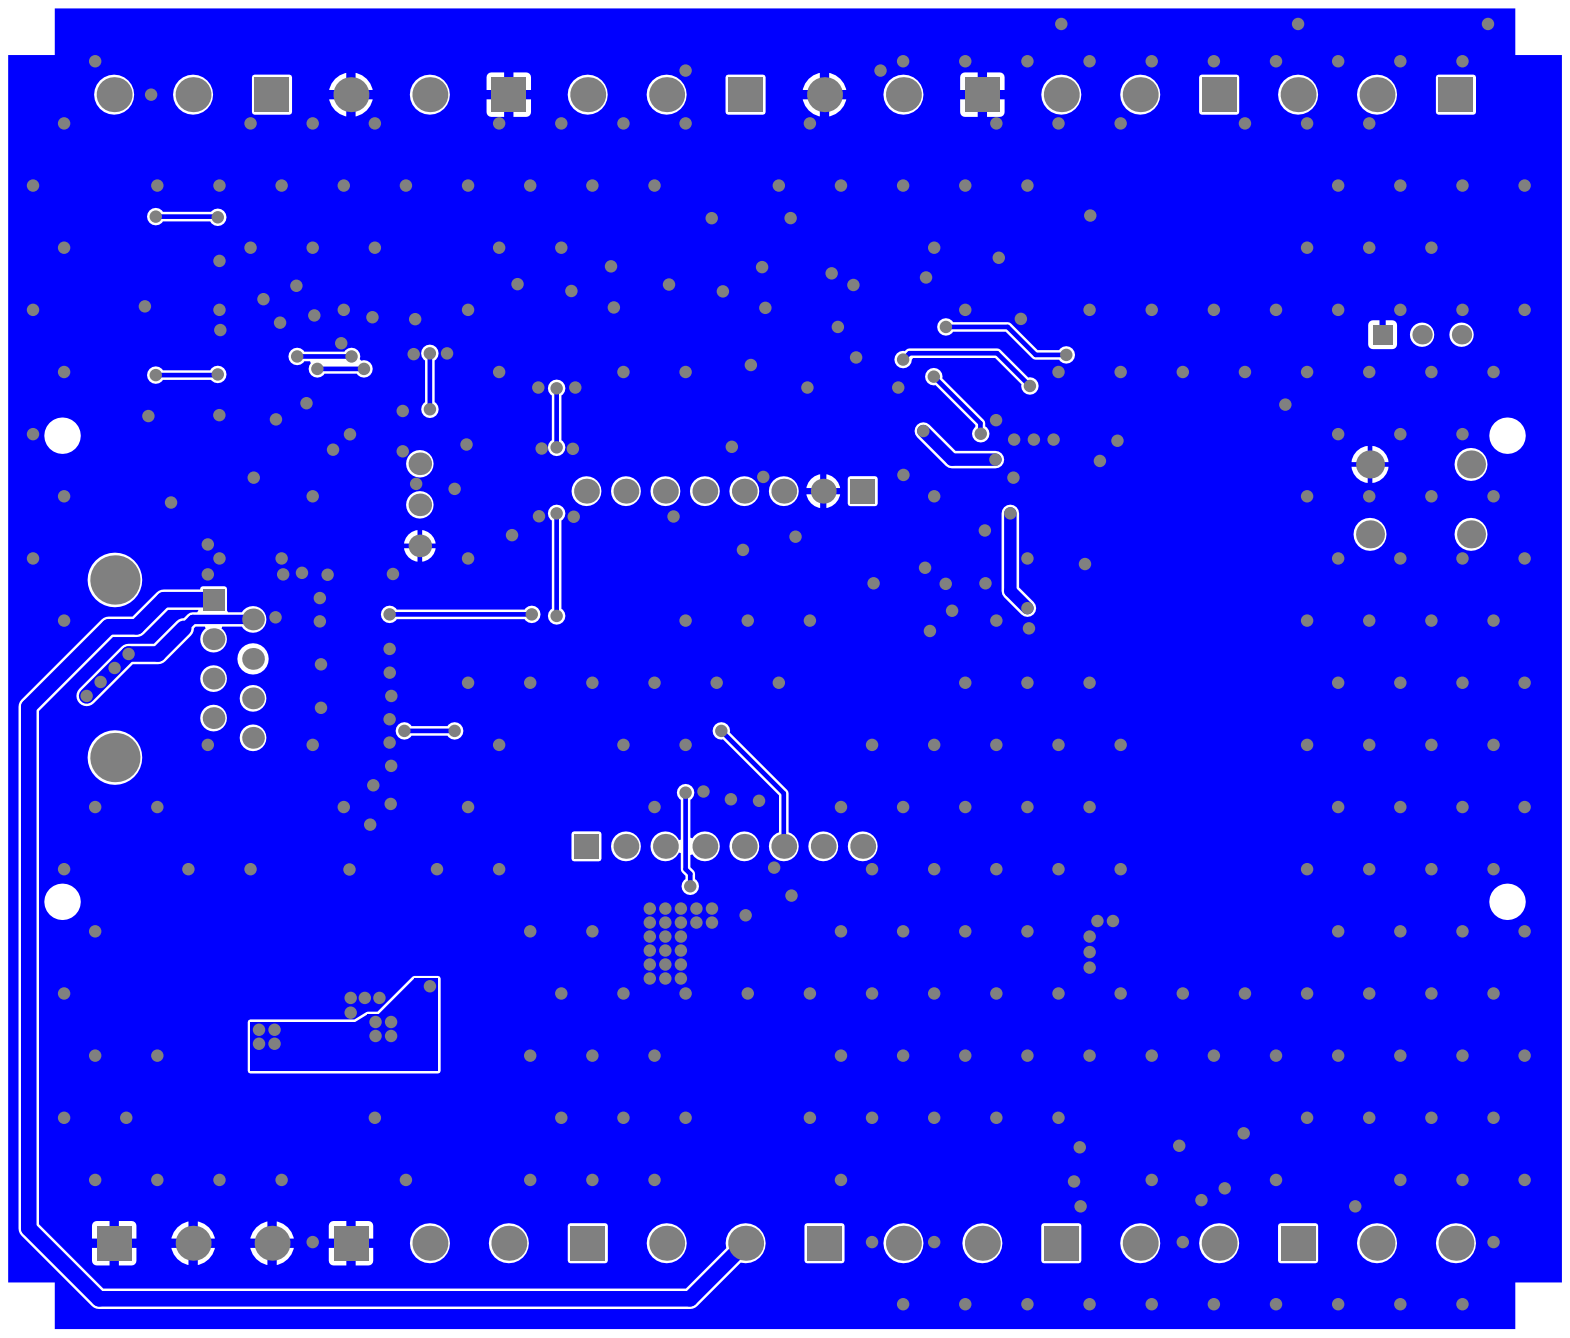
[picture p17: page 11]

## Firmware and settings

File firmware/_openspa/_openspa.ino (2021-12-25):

#include "_openspa.h"
#include "console.h"
#include "io.h"
#include "onewire.h"
#include "io_expander.h"
#include "pwm.h"
#include "hot_tub.h"
#include "balboa_display.h"
#include "wifi.h"

#define TIMER_INTERVAL_MS        10

hot_tub jacuzzi(epin_o_main,    epin_o_heater,          epin_o_circulation_pump,
                epin_o_pump_1,  epin_o_pump_1_speed,    epin_o_pump_2,
                epin_o_blower,  epin_o_ozone_generator, epin_o_light,
                epin_i_pressure_switch);

balboa_display bb_display(pin_o_bb_display_data_out, pin_i_bb_display_data_in, pin_o_bb_display_clock);

uint8_t openspa_error = 0;

void setup()
{
  consoleInit();
  ioInit();
  ioExpanderInit();
  pwmInit();
  jacuzziInit();
  if (openspa_wifi_enable)
    wifiInit();
  delay(10);
  consolePrintCommands();
}

void loop()
{
  if (openspa_wifi_enable)
    wifiHandler();

  openspaErrorHandler();

  openspa_error = jacuzzi.poll();

  displayHandler();
  consoleHandler();

  onewire_poll();
  //oneWireSearch(); //You can use this function to search for new onewire devices and add the address in _openspa.h file

  #ifdef ESP8266
    yield();
  #endif
}

uint8_t jacuzziInit()
{
  jacuzzi.setMaxTemperature(openspa_max_temperature);
  jacuzzi.setMinTemperature(openspa_min_temperature);
  jacuzzi.setDesiredTemperature(openspa_init_desired_temp);

  jacuzzi.setMaxTotalPower(openspa_power_total_max);
  jacuzzi.setHeaterPower(openspa_power_heater);
  jacuzzi.setCircPumpPower(openspa_power_pump_circ);
  jacuzzi.setPump_1_Power(openspa_power_pump_1);
  jacuzzi.setPump_2_Power(openspa_power_pump_2);
  jacuzzi.setBlowerPower(openspa_power_blower);

  jacuzzi.setPump_1_Timing(openspa_runtime_pump_1, openspa_resttime_pump_1);
  jacuzzi.setPump_2_Timing(openspa_runtime_pump_2, openspa_resttime_pump_2);
  jacuzzi.setBlowerTiming(openspa_runtime_blower, openspa_resttime_blower);

  jacuzzi.setFilteringSettings(openspa_filter_window_start_time, openspa_filter_window_stop_time, openspa_ozone_window_start_time,
                       openspa_ozone_window_stop_time, openspa_filter_daily_cycles, openspa_filter_time);
  jacuzzi.setHeatingSettings(openspa_heating_pwm, openspa_heating_min_power, openspa_heating_timeout, openspa_heating_timeout_delta_degrees);
  jacuzzi.setFlushingSettings(openspa_flush_window_start_time, openspa_flush_window_stop_time, openspa_flush_daily_cycles,
                      openspa_flush_time_pump_1, openspa_flush_time_pump_2, openspa_flush_time_blower);

  return 0;
}

uint8_t openspaErrorHandler()
{
  static uint8_t io_expander_reset_state_prv = true;

  if ((io_expander_reset_state_prv == false) and (ioReadIOExpanderReset() == true)) //Reinit when reset is released (error reset button on pcb)
  {
    delay(10);
    io_expander_reset_state_prv = false;
    openspaReset();
  }

  io_expander_reset_state_prv = ioReadIOExpanderReset();

  if (io_expander_reset_state_prv == false)
  {
    openspa_error = 255; //External error (Heater overtemp)
  }

  return 0;
}

void openspaReset()
{
  ioExpanderInit();
  digitalWrite(pin_o_io_expander_reset, HIGH);
  jacuzzi.reset();
  openspa_error = 0;
}

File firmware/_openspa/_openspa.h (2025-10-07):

//WiFi, NTP settings
const uint8_t   openspa_wifi_enable =     1;
#define         openspa_timezone          TZ_Europe_Brussels
#define         openspa_ntp_servers       "europe.pool.ntp.org", "time.nist.gov"

//Maximum - minimum temperatures
const float openspa_init_desired_temp   = 38.0;
const float openspa_max_temperature     = 45.0;
const float openspa_min_temperature     = 5.0;

//Heating
const uint16_t  openspa_heating_timeout                 = 3600; //seconds
const float     openspa_heating_timeout_delta_degrees   = 1.0;
const uint16_t  openspa_heating_window_start_time       = 1600; //hours:minutes -- not implemented yet
const uint16_t  openspa_heating_window_stop_time        = 2300; //hours:minutes -- not implemented yet
const uint8_t   openspa_heating_pwm                     = 1;    //control heater power through PWM using external PCA9685 and e.g. Kemo M150 + Kemo M028N
const uint8_t   openspa_heating_pwm_pca9685_address     = 0x40;
const uint16_t  openspa_heating_min_power               = 500;

//Filtering/flush timing
const uint16_t openspa_filter_window_start_time  = 900;  //hours:minutes
const uint16_t openspa_filter_window_stop_time   = 2000; //hours:minutes
const uint16_t openspa_ozone_window_start_time   = 1100; //hours:minutes
const uint16_t openspa_ozone_window_stop_time    = 1600; //hours:minutes
const uint16_t openspa_filter_daily_cycles       = 4;
const uint16_t openspa_filter_time               = 3600;    //seconds

const uint16_t openspa_flush_window_start_time   = 1000; //hours:minutes
const uint16_t openspa_flush_window_stop_time    = 1800; //hours:minutes
const uint16_t openspa_flush_daily_cycles        = 3;
const uint16_t openspa_flush_time_pump_1         = 60;   //seconds
const uint16_t openspa_flush_time_pump_2         = 60;   //seconds
const uint16_t openspa_flush_time_blower         = 10;   //seconds

//Maximum run time and rest time for pumps and blower in seconds
const uint16_t openspa_runtime_pump_1      = 900;  //seconds
const uint16_t openspa_resttime_pump_1     = 60;   //seconds
const uint16_t openspa_runtime_pump_2      = 900;  //seconds
const uint16_t openspa_resttime_pump_2     = 60;   //seconds
const uint16_t openspa_runtime_blower      = 300;  //seconds
const uint16_t openspa_resttime_blower     = 60;   //seconds

//Power in Watts - not implemented yet
const uint16_t openspa_power_total_max     = 3600;
const uint16_t openspa_power_heater        = 2200;
const uint16_t openspa_power_pump_circ     = 400;
const uint16_t openspa_power_pump_1        = 1200;
const uint16_t openspa_power_pump_2        = 500;
const uint16_t openspa_power_blower        = 500;

//OneWire

const uint8_t openspa_onewire_temp_sensor_1_enable = 1;
const uint8_t openspa_onewire_temp_sensor_1_address[8] = {0x28, 0x45, 0x51, 0x13, 0x0C, 0x00, 0x00, 0xD3};

const uint8_t openspa_onewire_temp_sensor_2_enable = 1;
const uint8_t openspa_onewire_temp_sensor_2_address[8] = {0x28, 0x05, 0xBC, 0xAD, 0x3A, 0x19, 0x01, 0x1B};

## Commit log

2020-04-30 code cleanup, added hardware files
    [OpenSpa_BOM.xlsx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]
2020-05-01 Added running average to thermistor readout.
    Added holdoff to heating routine.
    Added max temperature readout.
    Renamed variables in hot tub class.
2020-05-07 Changed configTime init
    Changed configTime init for compatibility with esp8266 arduino core v2.7.0
    Moved firmware files to _openspa folder
2020-05-26 Code cleanup
    Changed some timing variables from uint16 to unsigned long to avoid any overflow.
    [_openspa.h, _openspa.ino, hot_tub.h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]
2020-06-02 Added separate flush times for pumps and blower
    Added separate flush times for pumps and blower
2020-08-06 Changed temperature display
    Display desired temperature when current temperature is within 0.5 degrees of desired temperature.
2020-09-19 Seperate flush times for pumps and blower
    Seperate flush times for pumps and blower
2021-03-06 Added heating enable/disable
    Added heating enable/disable through homie
2021-03-22 Added heating on/off
    Added heating on/off
    Added heating on/off for improving self usage of solar power.
    Fixed bug in error checking (= -> ==)
    Added state machine for relay output control, main relay is switched off when no other relays are on.
    Removed this-> reference in all files.
    [_openspa.ino, balboa_display.ino, console.ino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]
2021-12-25 Added support for PCA9685 PWM driver for variable heating power.
    Added support for PCA9685 PWM driver for variable heating power.
2025-10-07 Added reset over mqtt
    Added reset over mqtt
    [_openspa.h, console.ino, hot_tub.h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]
